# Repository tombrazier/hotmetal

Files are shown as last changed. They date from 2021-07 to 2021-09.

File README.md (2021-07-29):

# Hot Metal Brewbot

This project started as an Arduino PID controller for my coffee machine and gradually became a lot more. Read about it [here](http://tomblog.firstsolo.net/index.php/hobbies/pimping-my-coffee-machine/). See a video of the machine in action [here](https://www.youtube.com/watch?v=up54jM5fQOQ).

Presently there is just a controller PCB and firmware. In time I plan to build a front panel PCB as well. The board is designed to mount neatly in a Gaggia Baby machine but there is scope for other layouts for different machines. The circuit diagram would work with pretty much all machines with some modifications to the firmware.

`hardware/controller` contains EAGLE CAD files for the controller PCB which is an Arduino Nano shield.

`hardware/schematics` contains PDFs of the schematics for release versions of the controller. Saves hacing to have EAGLE installed and also gives past versions.

`firmware/controller` contains the Arduino source code.

`hardware/controller/DesignNotes.txt` contains a lot of useful information as well as notes about what needs doing next.

The present revision of my controller is 2.0, but I already know of some things I would like to change in 2.1. `DesignNotes.txt` documents these.

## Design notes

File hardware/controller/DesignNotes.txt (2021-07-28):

CHECKS before send board to print
---------------------------------
Y is board labeled with name and revision?
Y make sure all text is vector font (Options->User Interface->Always use vector fonts. Because Eagle stupidly offers proportional font it cannot render to gerber files!)
Y check ERC
Y set up DRC rules (using JLCPCB for fab?)
Y renumber components
N check that track layout and board mounting prevent a water leak from conducting live to the user
Y check through-hole components are on the right side of the board (top, i.e. not mirrored)
Y check label placements (not covered by components or clashing with each other)
Y check labels are not covering pads
Y check labels are on the correct layer (i.e. blabel / tlabel)
Y check pins are labelled where necessary (incl Live, Neutral, Earth)
Y check component sizes vs stock (e.g 1uF 0603 ceramic cap)
Y check the specific components are available to buy (e.g. regulators)
Y check USB cable clearance (11mm above board, 9.8mm wide, 28mm long)
Y check IO pins are on a 0.1" grid
Y check heatsink placements
Y check no components that collide with the vertical columns on machine base plate back side (0.8" to 1.1" and 2.8" to 3.1" from bottom right, height 0.8")
Y check no components that collide with the vertical columns on machine base plate front side (3.45" to 3.7" from bottom right, height 0.6")
Y check all airwires routed (Tools -> Statistics gives number of unrouted airwires)
Y check mains power nets are in net class power (see what breaks min width 50mil and 1.6mm separation from default class and 1mm separation for power class)
Y check DRC (with appropriate layers visible otherwise they don't get checked - note label layers are best checked visually and stop layers should be checked)

Errors/notes:
-------------
-Space for an onboard fuse? (For Non-UK plugs).
-Onboard varistor.
-D2 is physically close to the tray and a deep pool of water could connect to mains. Exposed GND along
 top and bottom sides of the board at the lower edge (in HEATSINK component) would mitigate as well.)
-Move zero cross circuit to 9V side of transformer and use JFET! (MMBFJ201 would need no resistor).
 -R43 should be 1206 not 0805 to handle 400V.
 -The R43 / C26 RC circuit is really an RLC circuit when stray (e.g. house) inductance is taken into account and
  can have inductance in the 10s of uH. If the circuit is underdamped, this can result in destructive voltage spikes.
-PMPSW and STMSW are wrong way round considering line to IC2. Also it's a lot easier if software
 controls the temperature probe ranges so use D10 (SS) pin for PMPSW.
-Buzzer FET should have gate pulldown for when AVR is resetting and pin output is open.
-R10/R11 potential divider relies on 5V which is unreliable, e.g. when on USB - use zener or regulator or something
 (MMBFJ201 if using it for zero crossover)
-There is never a need for VSS < 0V even with K type. Eliminate -ve supply.
-Since VDD > 5V (i.e. arduino VCC), opamp outputs to the arduino should have resistors on them.
-Coupling between VSS / VDD and the inputs to the opamp. Route lines differently.
 -Piezo buzzer puts noise on the VDD line.
 -I changed C12 to 1uF 16V and doubled up C5.
 -Since we really don't care about an high frequency signal, why not put a cap between opamp +ve and -ve inputs?
-LED markings have no polarity.
-Provision for NTC probes is poor.
-Terminal markings should be repeated on underside of board.
-The USB 5V supply can be quite noisy at highish frequency (e.g. 50kHz) and this
 noise is conducted progressively to ground in the probe pin decoupling caps and C25,
 causing a differential voltage across the probes. Only an issue when mains power off.
 Whichever of SJ1-SJ4 is used, it should be a 2k2 resistor, not a bridge.
-The AREF pins sucks in about 50uA, which makes the probe current about 5% over target
 and shifts the temperature ranges downwards a bit. Not really an issue but it means
 a nominal 100R resistor probably has an input > 0 and a 150R nominal is 1023 (i.e.
 maxes out the ADC.
-With K type probe, an additive component would allow for probe to be cooler than AVR
-With K type probe, the op amp's Vio is quite significant but results in a fixed delta. Unfortunately this varies by 7uV/C which is significant at a range or 50C. 
-With K type probe, internal temp reference is sensitive to VCC. So you get a different reading if powered by USB vs mains.
 So is bandgap, to a similar degree, divide by BG to offset the change.
-With K Type, internal temp is bady affected by self-heating of the AVR.
-With K type probe, internal temp has occasional wild excursions.

TODO:
-----
Build: make cable for Twin front panel using an Amp-TE Micro-Match 14 way ribbon connector but with 4 strands of wire.
Plastic backing plane.
internal LEDs for when front panel is perspex?

Spacing, etc. (PCBWay recommendations)
--------------------------------------

Min recommended track width: 6mil.
Min recommended spacing:     6mil.
Min drill size:              0.2mm (8mil) (but 0.3mm costs less).
Min annular ring:            0.15mm (6mil) (so total via diameter >= 0.3mm larger than hole).

Build notes
-----------

C20, C22, SJ1 to SJ7 give options to connect thermocouples or resistive
deivces (e.g. PT100 probes) to probes 1 to 3. For PT100, SJ1 and SJ5 to
SJ7 are be bridged and the rest unbriged/unpopulated. But if using
thermocouples rather than PT100s, some of the jumpers are unbridged
and some of the resistors and capacitors are populated. The resistor
network on the opamps would also have to change.

Displays
--------

OLED modules that use I2C or SPI look like a good option. E.g. the waveshare 1.5inch OLED
display. OLED and TFT displays us on the order of 30mA with all pixels illuminated.

Heat and heatsinksing
------------

Problem environment: both chambers inside the machine are spaces for
boilers and so hot environments. Depending on location, it could be as
hot as 70C.

The bottom of the board is shielded from heat by the board itself and is
also adjactent to the case. This will be the coolest spot.

High power components need to be on the bottom of the board. E.g. regulators
and constant current depletion mode FET in the zero-crossover circuit.

TRIAC thermal runaway: any temperature over 125C causes the TRIACs to
switch on permanently, which means everything will just keep getting hotter
until something burns. So TRAIC cores MUST remain < 125C. So 115C for safety.
So we have a headroom of 45K.

Current: maximum continuous power demand is when steaming milk. For a
decent flow of steam (3 nozzle), about 2kW is desirable. At 240VAC, that
means 8.3A and for TRIACs that means about 8W.

Heatsinks: the chunkiest passive heatsinks for TO-220 packages tend towards
10K/W. At a headroom of 45K, that means we can cool 4.5W. This is less than
the 8.3W we need to cool!

Solution: a happy circumstance is that continuous 8.3W power drain only
occurs when water is flowing through the machine. So, an easy answer is
to use a water-cooled CPU heatsink connected inline with the supply water.
This arrangement will need to be on some kind of bracket to keep it in place.
But the board, as a whole, need to be on a bracket to keep it in place.
A copper sheet between the heatsink and the TRAICs can have a double function
of bracket and heatpipe. Best of all, no power is wasted as the waste heat
becomes a slight preheat for the water!

Analogue sensors
----------------

Aref given by a voltage regulator:
    -Needs to be exact.
    -Needs to be stable over temperature range. Although the most important
     measurements are from the PT100 devices, which are in-line and Aref
     scales with PT100 voltage and stability isn't important.
    -If in-line with PT100 devices, adjust pin current needs to be tiny.

MCP1700T-1802E/TT has very small GND current (MOSFET device) and reasonable stability
over temperature.

Place regulator on bottom of board for minimal effect from boiler heat.

Steam switch can be used to provide an input to op-amps that shifts PT100 range.

Main boiler sensors
-------------------

These need to be the most accurate of all the sensors so we can set brew
temperature to within a fraction of a degree. The resistor network converts
the probe voltage range for 120C to a range of 1.8V (which is what Aref gets
from the 1.8V regulator) and subtracts the equivalent of 100Ohms which is
the PT100 value for 0C.

When the steam switch is closed, an analogue switch brings another resistor
into the network, subtracting an extra voltage from the output and shifting
the measurement range.

Water level gauge
-----------------

MPXV7002 works nicely.
(https://www.nxp.com/docs/en/data-sheet/MPXV7002.pdf)

The reservoir is empty when there is about 5cm head of water = 0.5kPa and
full when there is about 5cm head of water = 1.5kPa. These pressures equate
to an output voltage of 3V to 4V (at supply voltage of 5V and linearly scaled
against the supply).

Variations in atmospheric pressure cause the max and min values to change
so we need some space around these points. If we allow a range of 2.5V to
4.5V, then 1 bit from the 10 bit ADC equates to about 0.2% of the reservoir,
which is a resultion greater than measurement error.

Vref is attached to 1.8V which implies the need for a gain of less than unity,
which makes op-amp instability likely. We can acheive this with a potential
divider to zero on both +ve and -ve inputs to the op amp.

                  |\
Vp ---[ R1 ]------|+\
GND---[ R2 ]-'    |  \______Vo
                  |  /    |
5v ---[ R3 ]------|-/     |
GND---[ R4 ]-|    |/      |
             L---[ R5 ]---'

R1=100k, R2=10k, R3=100k, R4=4k7, R5=33k gives a pretty good range from
Vp = 2.17V to 4.54V.

Zero-crossover
--------------

The zero-crossover circuit uses a diode in series with an opto-coupler to
signal from the mains voltage side to the logic voltage side that mains
is above a few volts. The opto-coupler is connected directly to an arduino
pin with an internal pull-up.

This has a nice advantage that the on and off times are slightly different
because mains voltage has to be about two diode drops above zero for the
opto-coupler to switch on enough. With suitable calibration, mains voltage
can therefore be measured, which can make power calculations even more accurate.
This is overkill and, therefore, strictly bad software engineering but it
feels strangely pleasing!

To keep the components safe, a depletion mode MOSFET and a resistor act
as a current-limiting circuit to keep the current below around 0.5mA.

The circuit as a whole needs to be protected from high frequency noise for
two reasons. First, noise can cause a zero-crossover in the wrong place.
Much more seriously, a high dV/dt on the MOSFET can destroy it.

There are two ways a MOSFET can be damaged by dV/dt. One is to do with the
parasitic BJT in combination with its base resistances and capacitances. This
is a hard limit of the device itself. The datasheet give a max of 6GV/s.

The other source of damage is when the maximum Vgs voltage is exceeded because
of gate capacitances. This depends on the device and also the external circuit.
In our circuit, a sudden change of voltage from operating the mains switch
mid-cycle is enough to cause this. It can happen with switching on or
off. Technical: mains voltage is applied across drain and gate with a resistor
between gate and source. The normal current path goes through this resistor.
But if there is a sudden 340V change on Vgd then the Cds and Cgs have to charge
to this voltage. According to the datasheet, Cds = Coss - Crs = 1.4pF and
Cgs = Ciss - Crss = 20pF. The voltage on source will change by 340 / (1 + Cgs / Cds)
with respect to gate which is about 22V. The absolute maximum Vgs is +/- 20V.

We can limit Vgs to +/-20V if we limit the current in the 2k2 gate source resistor
to about 9mA. For Cds to conduct that current, voltage across Cds has to be
changing at about 6.5GV/s. This is more than the datasheet's hard limit of 6GV/s, so
6GV/s is the limit.

A series RC filter can give this but can also introduce problems of its own.
Taking stray inductance into account, we have an RLC circuit. Depending on
the initial charge of the capacitor and the instantaneous mains voltage applied,
there can be oscillations that peak a lot higher than the mains voltage peak.
Worst case scenario, at -340V transformer stops conducting because bridge rectifier
on 9V side switches off and zero-cross circuit is reverse biased. Capcitor remains
charged to -340V and then 340V is applied. The resistor has to handle 680V and the
capacitor voltage swings to as much as 1020V! With just the right timing in switch
bounce this could happen!

Nonetheless, if switch on occurs at 340V and the RLC circuit is not well damped
then the initial oscillation can swing the voltage on the capacitor up to nearly 680V!
So the RLC circuit should be overdamped. i.e. R^2 > 4L/C. L can be as high as tens of
uH for 10m of copper wire - which is normal in house wiring.

A 100R resistor in series with a 500V 68nF capacitor will keep dV/dt low enough
and also easily overdamp a house with 100uH inductance in the wiring.

Better solution: move the zero-crossing circuit to the 9V side of the transformer
and use a JFET instead of a MOSFET and a schottkey diode for protection.

Arduino pins
------------

Avoid using the SDA and SCL (A4 and A5) pins so TWI is available (leave as general digital IO).
Avoid using the SS, MISO, MOSI and CLK pins so SPI is available (leave as general analogue IO).

The pump is driven by PWM, and needs to be on pin OC2B.
The solenoid can be on any digital pin as it is simply switched on and off.
The 2 boilers can be on any digital pin because they are driven by an interrupt function at each zero-crossover.
The 2 switches and 2 LEDs can be on any digital pin.
The analogue inputs should use at least pins A6 and A7 because these have no other function. There are three temp probes and a water level meter.
The flow meter can be on any pin with PCINT. Note: it's easier not to share these interrupts.
The mains zero crossover can be on any pin with PCINT. Note: it's easier not to share these interrupts.

Power supply
------------

Rev 1.0 draws around 70mA at its highest drain. Add another 8mA for the extra opto-couple
in Rev 2.0 and another 40mA for the mood lighting LEDs and we need about 120mA.

For interfacing with the Baby Twin's hardware, we need another 78mA. The
front panel uses 75mA with all LEDs illuminated and the hall effect sensor
(steam switch) uses 3mA.

A home made front panel would need something like 30mA per OLED or TFT display
and 20mA for an arduino. So 80mA.

On the plus side, removing the Baby Class front panel takes us down two LEDs
or 20mA.

So the heaviest load I imagine is 120mA plus about 80mA for a front panel
minus 20mA. We need to be able to cover 180mA comfortably.

Under maximum current on Rev 1.0, the ripple dips to just under 9V. Rev 2.0's schottkey bridge
rectifier drops less voltage than Rev 1.0's oversized 400V 1A S1G rectifier. Rev 2.0 uses a
bridge rectifier whereas Rev 1.0 used a single diode for single-phase rectification
(which made the Rev 1.0 zero-crossover circuit possible - Rev 2.0 has a different arrangement). So
the same capacitance on Rev 2.0 will give half the ripple at the same current as Rev 1.0.

We need a minimum of about 8.5V for the 8V regulator's dropout.

We can suppose, based on the above, that 1000uF will drop to 9V at 140mA. Another 50mA would
drop the 1000uF capacitor by 0.5V in 10ms. So we should be able to get 190mA. That's
okay.

TRIACs
------

Temperature inside top housing gets to as much as 50K above ambient, i.e.
in the 70s C.

Max temp for TRIAC is 125C.

Requirements for TRIACs / SCRs:
    -Isolated tab.
    -Blocking voltage > +-340V.
    -Current limit high enough.
    -Power dissipation small enough (see note).

Boiler SCR power note:
    RMS boiler current is mains voltage over resistance:
        Ib(RMS) = 240 / 21.5 = 11.2A
        Ib(AV) = Ib(PEAK) * 0.637 = Ib(RMS) * 1.414 * 0.637 = 10.1A
    Each SCR only conducts for half of each AC cycle so:
        I(RMS) = Ib(RMS) * 0.707 = 7.9A
        I(AV) = Ib(AV) / 2 = 5.0A
    That's assuming the datasheet gives power over the whole AC cycle even
    though an SCR conducts for only up to half the cycle. If it gives power
    just for the half-cycle where it conducts, then we need to read off power
    against the full current (RMS or AV) and halve it.

For the boiler, the gate of the SCR needs to be protected from negative
bias by a diode. Given this, we could just as well use a TRIAC if it is
convenient to do so.

For all the TRAICs / SCRs, the gate's current needs to be limited with a
resistor. A potential divider is unneccesary, though, because gate/cathode
is a PN juntion (i.e. a diode) and so it's voltage is limited to the diode
turn on voltage.

For the boiler:
TXN612 SCR is insulated, blocks 600V, carries 8A average and generates 6W at I(AV)=5A.
BTA24-600BWRG or BTA24-800BWRG TRIACs also meet all the criteria for the boiler.

For pump and solenoid:
BTA08-600CWRG TRIAC is sufficient and insulated.

Gaggia Baby Twin front panel interface
--------------------------------------

Note: for testing purposes, the Twin controller board has an 8 pin header which
includes a GND pin:

    JP7
    -  -
    -  -
    -  -
    -  - GND

A 14 wire ribbon cable connects the front panel to the controller board. If we
number the wires from 1 to 14, starting at the red end, then the connector
on the board alternates sides:

14  12  10   8   6   4   2
 |   |   |   |   |   |   |
-----------------------------
|                           ]
|                          |
|                           ]
-----------------------------
   |   |   |   |   |   |   |
  13  11   9   7   5   3   1

The connector is from te (Tycho Electronics) and the ribbon cable part
number is 1-215083-4 or 8-215083-4 (same part but one comes in boxes and
the other on reels).

My best guess is that the controller board has two interfaces on this cable,
one for the Twin and one for the Dose. For the Twin, it is a TWI interface
and for the Dose it is a simple set of lines to LEDs and switches. The only
pins that seem to make any difference for the Twin are:

1  VCC
9  SDA
7  Button touch notification
11 SCL
14 GND

The front panel pulls pins 9 (SDA), 11 (SCL) and 7 high. When a button is
touched or released, pin 7 pulses low for 50us. This could be used to respond
or you can you poll regularly.

In addition, the controller board pulls the following high: 2, 4, 6, 8, 10.
And 3 and 5 are high impedence. And 12 is low or high impedence (can't remember).
None of these are relevant to the Twin front panel.

The controller polls the front panel periodically with the following protocol:
Poll rate: normally every 48ms. When a button is being touched, continuously.
SCL clock speed: 62500Hz.

At each poll, the controller writes the LED state and then reads the buttons.

To write: write two bytes, the first is address and the second is value.
To read: write one byte (address) and read one byte (value).
The front panel only responds to the general call TWI address 0.
The address of the LEDs is 0x00 and the address of the buttons is 0x01.

So on the TWI bus, you see:
START, address packet to 0 and W = 0x00, 2 data packets: 0x00, CODE1, STOP,
START, address packet to 0 and W = 0x00, 1 data packets: 0x01, STOP,
START, address packet to 0 and R = 0x01, 1 data packets: CODE2, STOP.

CODE1 is a six bit bitmask plus two parity bits:

| 7        | 6        | 5           | 4         | 3         | 2          | 1         | 0         |
| Parity 1 | Parity 0 | Element LED | Steam LED | Water LED | Manual LED | 2 cup LED | 1 cup LED |

Parity 1 is bit3 XOR bit4 XOR bit5.
Parity 0 is bit0 XOR bit1 XOR bit2.

CODE2 is a pair of 4 bit nibbles where high nibble = 1s complement of low nibble.
Low nibble is a 4 bit bitmask indicating which button is touched:

| 3     | 2      | 1     | 0     |
| Water | Manual | 2 cup | 1 cup |

Note: if more than one button is touched, this is invalid and code2 = 0xf0.

Front panel dimensions
----------------------

outer rect wxh: 108x68
this includes a 2.5mm deep tab at the top which is 6mm high
tabs on sides: 16 to 27 mm from bottom
inner rect wxhxd: 93.5x79x3
circle dia x d: 78x1.4

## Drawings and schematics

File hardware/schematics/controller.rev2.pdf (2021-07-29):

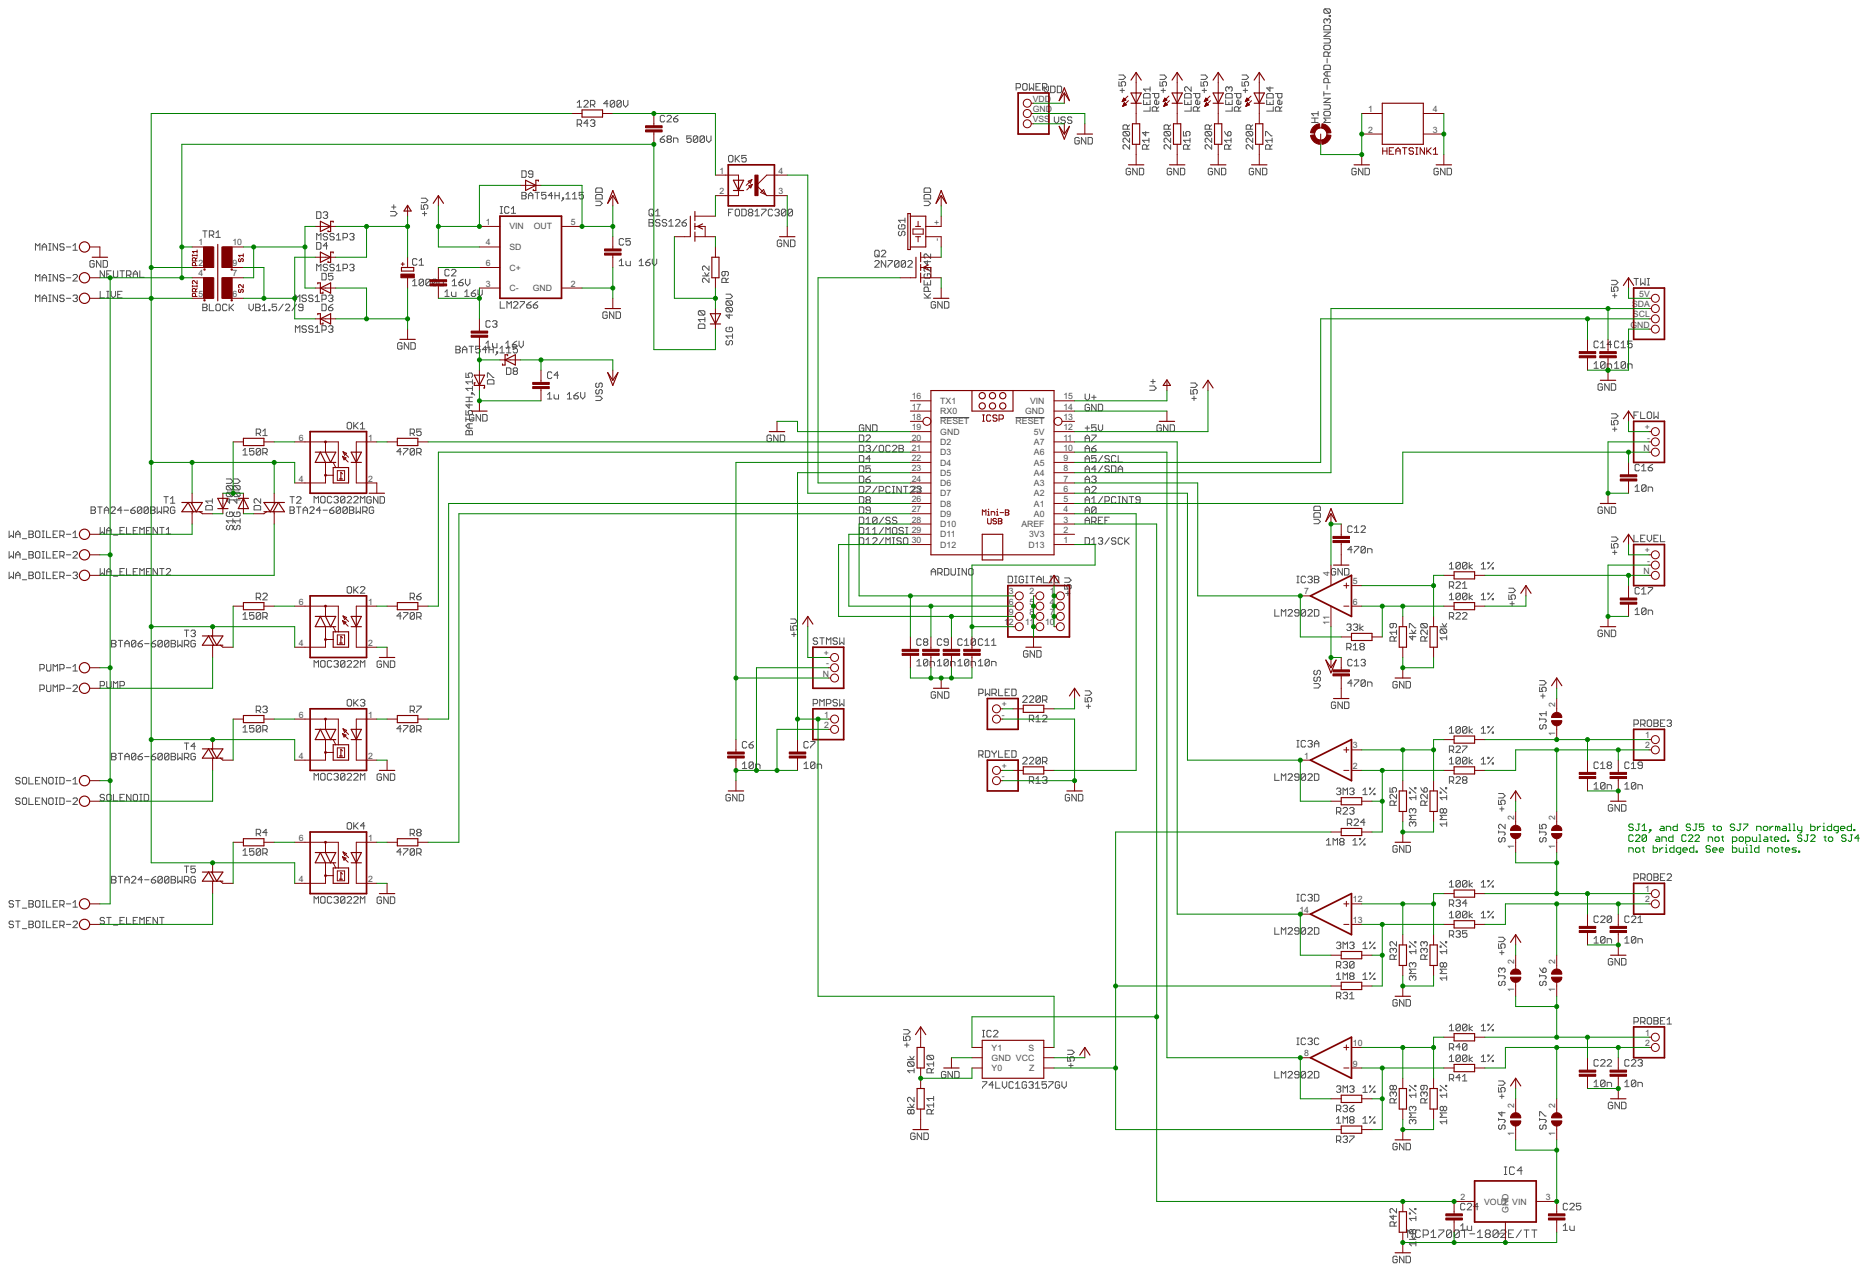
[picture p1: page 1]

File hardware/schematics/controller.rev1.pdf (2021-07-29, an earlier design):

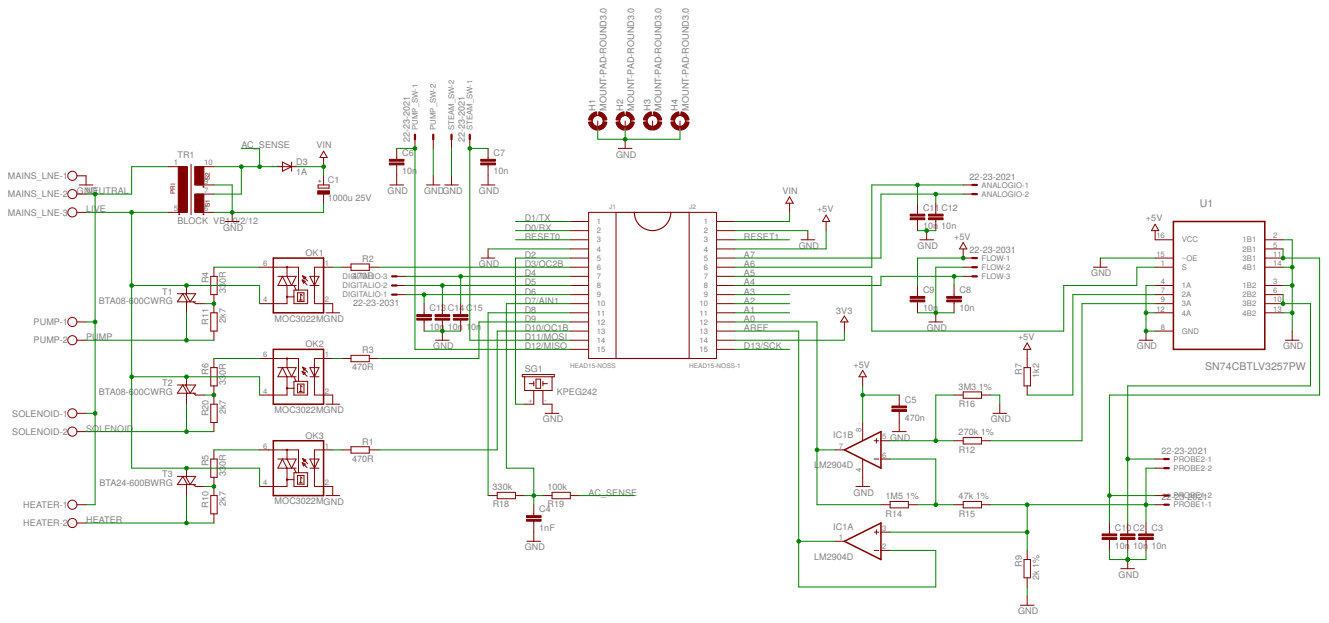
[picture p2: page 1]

MOUNT-PAD-ROUND3.0 MOUNT-PAD-ROUND3.0

1 | 14

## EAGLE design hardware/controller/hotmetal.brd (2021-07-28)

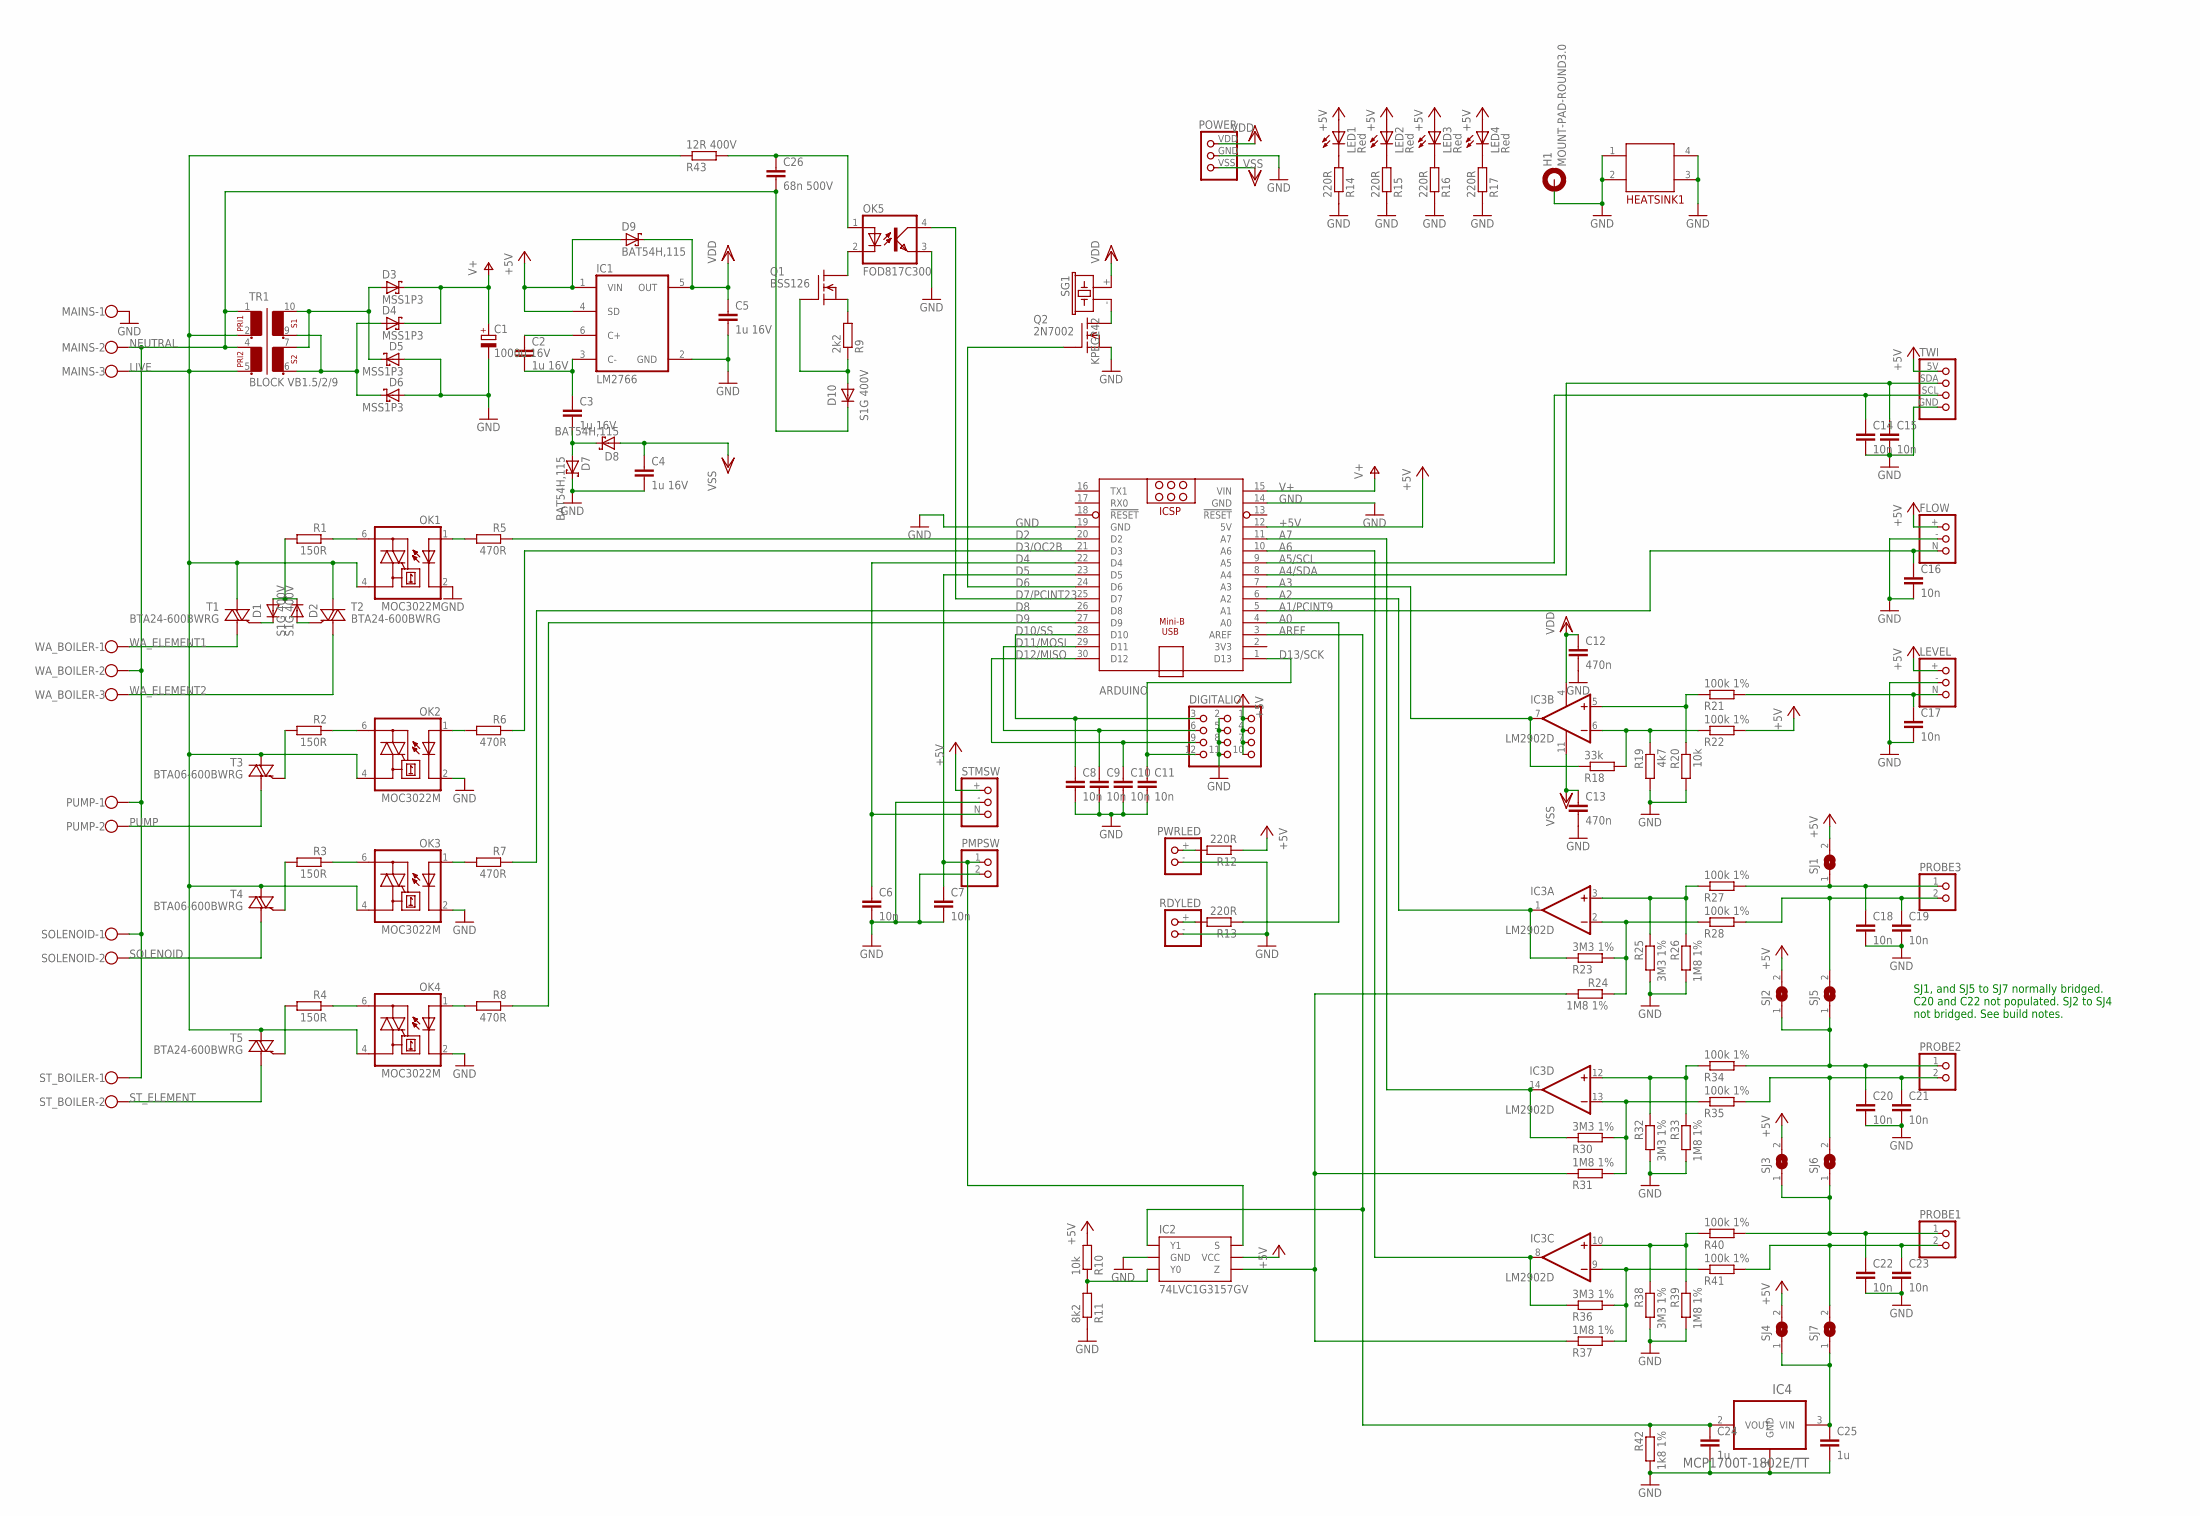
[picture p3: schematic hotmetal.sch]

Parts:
ARDUINO: ARDUINO_NANO
C1: 1000u 16V; E5-10,5
C2, C3, C4, C5: 1u 16V; C0603K
C6, C7, C8, C9, C10, C11, C14, C15, C16, C17, C18, C19, C20, C21, C22, C23: 10n; C0603K
C12, C13: 470n; C0603K
C24, C25: 1u; C0603K
C26: 68n 500V; C1210K
D1, D2, D10: S1G 400V; DO214AC
D3, D4, D5, D6: MSS1P3; POWERDI323
D7, D8, D9: BAT54H,115; SOD123F
DIGITALIO: HDR4X3PWR
FLOW: HDR3PWR
H1: MOUNT-PAD-ROUND3.0; 3,0-PAD
HEATSINK1: HOTMETALHEATSINK
IC1: LM2766; SOT23-6
IC2: 74LVC1G3157GV; SOT457
IC3: LM2902D; SO14
IC4: MCP1700T-1802E/TT; SOT23
LED1, LED2, LED3, LED4: Red; SML0805
LEVEL: HDR3PWR
MAINS: W237-103
OK1, OK2, OK3, OK4: MOC3022M; DIL06
OK5: FOD817C300; DIL04
PMPSW: HDR2
POWER: HDR3VDDVSS; HDR2VDDVSS
PROBE1, PROBE2, PROBE3: HDR2
PUMP: W237-102
PWRLED: HDR2PWR
Q1: BSS126; SOT23
Q2: 2N7002; SOT23
R1, R2, R3, R4: 150R; 0204/7
R5, R6, R7, R8: 470R; R0805
R9: 2k2; R0805
R10, R20: 10k; R0805
R11: 8k2; R0805
R12, R13, R14, R15, R16, R17: 220R; R0805
R18: 33k; R0805
R19: 4k7; R0805
R21, R22, R27, R28, R34, R35, R40, R41: 100k 1%; R0805
R23, R25, R30, R32, R36, R38: 3M3 1%; R0805
R24, R26, R31, R33, R37, R39: 1M8 1%; R0805
R42: 1k8 1%; R0805
R43: 12R 400V; R0805
RDYLED: HDR2PWR
SG1: KPEG242; F/CM12P
SJ1, SJ2, SJ3, SJ4, SJ5, SJ6, SJ7: SJ
SOLENOID: W237-102
STMSW: HDR3PWR
ST_BOILER: W237-102
T1, T2, T5: BTA24-600BWRG; TO220FACEDOWN
T3, T4: BTA06-600BWRG; TO220FACEDOWN
TR1: BLOCK VB1.5/2/9; T2P2S
TWI: HDR4TWI
WA_BOILER: W237-103

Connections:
+5V: ARDUINO.12 (5V), D9.A, DIGITALIO.1, DIGITALIO.4, DIGITALIO.7, DIGITALIO.10, FLOW.+ (1), IC1.1 (VIN), IC1.4 (SD), IC2.5 (VCC), LED1.A, LED2.A, LED3.A, LED4.A, LEVEL.+ (1), R10.2, R12.1, R22.2, SJ1.2, SJ2.2, SJ3.2, SJ4.2, STMSW.+ (1), TWI.5V (1)
A0: ARDUINO.4 (A0), R13.1
A1/PCINT9: ARDUINO.5 (A1), C16.1, FLOW.N (3)
A2: ARDUINO.6 (A2), IC3.1 (OUT), R23.1
A3: ARDUINO.7 (A3), IC3.7 (OUT), R18.1
A4/SDA: ARDUINO.8 (A4), C15.1, TWI.SDA (2)
A5/SCL: ARDUINO.9 (A5), C14.1, TWI.SCL (3)
A6: ARDUINO.10 (A6), IC3.8 (OUT), R36.1
A7: ARDUINO.11 (A7), IC3.14 (OUT), R30.1
AREF: ARDUINO.3 (AREF), C24.1, IC2.1 (Y1), IC4.2 (VOUT), R42.1
D2: ARDUINO.20 (D2), R5.1
D3/OC2B: ARDUINO.21 (D3), R6.1
D4: ARDUINO.22 (D4), C6.1, STMSW.N (3)
D5: ARDUINO.23 (D5), C7.1, IC2.6 (S), PMPSW.1
D6: ARDUINO.24 (D6), Q2.1 (G)
D7/PCINT23: ARDUINO.25 (D7), OK5.4 (COL)
D8: ARDUINO.26 (D8), R7.1
D9: ARDUINO.27 (D9), R8.1
D10/SS: ARDUINO.28 (D10), C8.1, DIGITALIO.3
D11/MOSI: ARDUINO.29 (D11), C9.1, DIGITALIO.6
D12/MISO: ARDUINO.30 (D12), C10.1, DIGITALIO.9
D13/SCK: ARDUINO.1 (D13), C11.1, DIGITALIO.12
GND: ARDUINO.14 (GND), ARDUINO.19 (GND), C1.-, C4.2, C5.2, C6.2, C7.2, C8.2, C9.2, C10.2, C11.2, C12.2, C13.2, C14.2, C15.2, C16.2, C17.2, C18.2, C19.2, C20.2, C21.2, C22.2, C23.2, C24.2, C25.2, D5.A, D6.A, D7.C, DIGITALIO.2, DIGITALIO.5, DIGITALIO.8, DIGITALIO.11, FLOW.- (2), H1.B3,0, HEATSINK1.1, HEATSINK1.2, HEATSINK1.3, HEATSINK1.4, IC1.2 (GND), IC2.2 (GND), IC4.1 (GND), LEVEL.- (2), MAINS.1, OK1.2 (C), OK2.2 (C), OK3.2 (C), OK4.2 (C), OK5.3 (EMIT), PMPSW.2, POWER.GND (2), PWRLED.- (2), Q2.2 (S), R11.1, R14.1, R15.1, R16.1, R17.1, R19.2, R20.2, R25.2, R26.2, R32.2, R33.2, R38.2, R39.2, R42.2, RDYLED.- (2), STMSW.- (2), TWI.GND (4)
LIVE: MAINS.3, OK1.4 (A1), OK2.4 (A1), OK3.4 (A1), OK4.4 (A1), R43.1, T1.T2 (A2), T2.T2 (A2), T3.T2 (A2), T4.T2 (A2), T5.T2 (A2), TR1.2, TR1.5
unnamed: OK3.1 (A), R7.2
unnamed: OK1.1 (A), R5.2
unnamed: OK4.1 (A), R8.2
unnamed: R3.2, T4.G
unnamed: OK3.6 (A2), R3.1
unnamed: D1.A, D2.C, R1.2
unnamed: R4.2, T5.G
unnamed: OK4.6 (A2), R4.1
unnamed: OK1.6 (A2), R1.1
unnamed: C21.1, PROBE2.2, R35.2, SJ6.2
unnamed: C22.1, PROBE1.1, R40.2, SJ3.1, SJ6.1
unnamed: C20.1, PROBE2.1, R34.2, SJ2.1, SJ5.1
unnamed: IC3.3 (+IN), R25.1, R26.1, R27.1
unnamed: D1.C, T1.G
unnamed: D2.A, T2.G
unnamed: C17.1, LEVEL.N (3), R21.2
unnamed: IC3.10 (+IN), R38.1, R39.1, R40.1
unnamed: IC3.9 (-IN), R36.2, R37.2, R41.1
unnamed: Q2.3 (D), SG1.- (2)
unnamed: LED3.C, R16.2
unnamed: C2.1, IC1.6 (C+)
unnamed: OK2.1 (A), R6.2
unnamed: R2.2, T3.G
unnamed: OK2.6 (A2), R2.1
unnamed: PWRLED.+ (1), R12.2
unnamed: R13.2, RDYLED.+ (1)
unnamed: C2.2, C3.1, IC1.3 (C-)
unnamed: C23.1, PROBE1.2, R41.2, SJ7.2
unnamed: C26.1, OK5.1 (A), R43.2
unnamed: D10.A, Q1.1 (G), R9.1
unnamed: C19.1, PROBE3.2, R28.2, SJ5.2
unnamed: C18.1, PROBE3.1, R27.2, SJ1.1
unnamed: IC3.12 (+IN), R32.1, R33.1, R34.1
unnamed: IC3.2 (-IN), R23.2, R24.1, R28.1
unnamed: IC3.13 (-IN), R30.2, R31.2, R35.1
unnamed: IC3.5 (+IN), R20.1, R21.1
unnamed: IC2.3 (Y0), R10.1, R11.2
unnamed: IC2.4 (Z), R24.2, R31.1, R37.1
unnamed: D3.A, D5.C, TR1.7, TR1.10
unnamed: IC3.6 (-IN), R18.2, R19.1, R22.1
unnamed: C25.1, IC4.3 (VIN), SJ4.1, SJ7.1
unnamed: LED1.C, R14.2
unnamed: LED2.C, R15.2
unnamed: LED4.C, R17.2
unnamed: D4.A, D6.C, TR1.6, TR1.9
unnamed: Q1.2 (S), R9.2
unnamed: OK5.2 (C), Q1.3 (D)
unnamed: C3.2, D7.A, D8.C
NEUTRAL: C26.2, D10.C, MAINS.2, PUMP.1, SOLENOID.1, ST_BOILER.1, TR1.1, TR1.4, WA_BOILER.2
PUMP: PUMP.2, T3.T1 (A1)
SOLENOID: SOLENOID.2, T4.T1 (A1)
ST_ELEMENT: ST_BOILER.2, T5.T1 (A1)
V+: ARDUINO.15 (VIN), C1.+, D3.C, D4.C
VDD: C5.1, C12.1, D9.C, IC1.5 (OUT), IC3.4 (V+), POWER.VDD (1), SG1.+ (1)
VSS: C4.1, C13.1, D8.A, IC3.11 (V-), POWER.VSS (3)
WA_ELEMENT1: T1.T1 (A1), WA_BOILER.1
WA_ELEMENT2: T2.T1 (A1), WA_BOILER.3

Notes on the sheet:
SJ1, and SJ5 to SJ7 normally bridged. C20 and C22 not populated. SJ2 to SJ4 not bridged. See build notes.

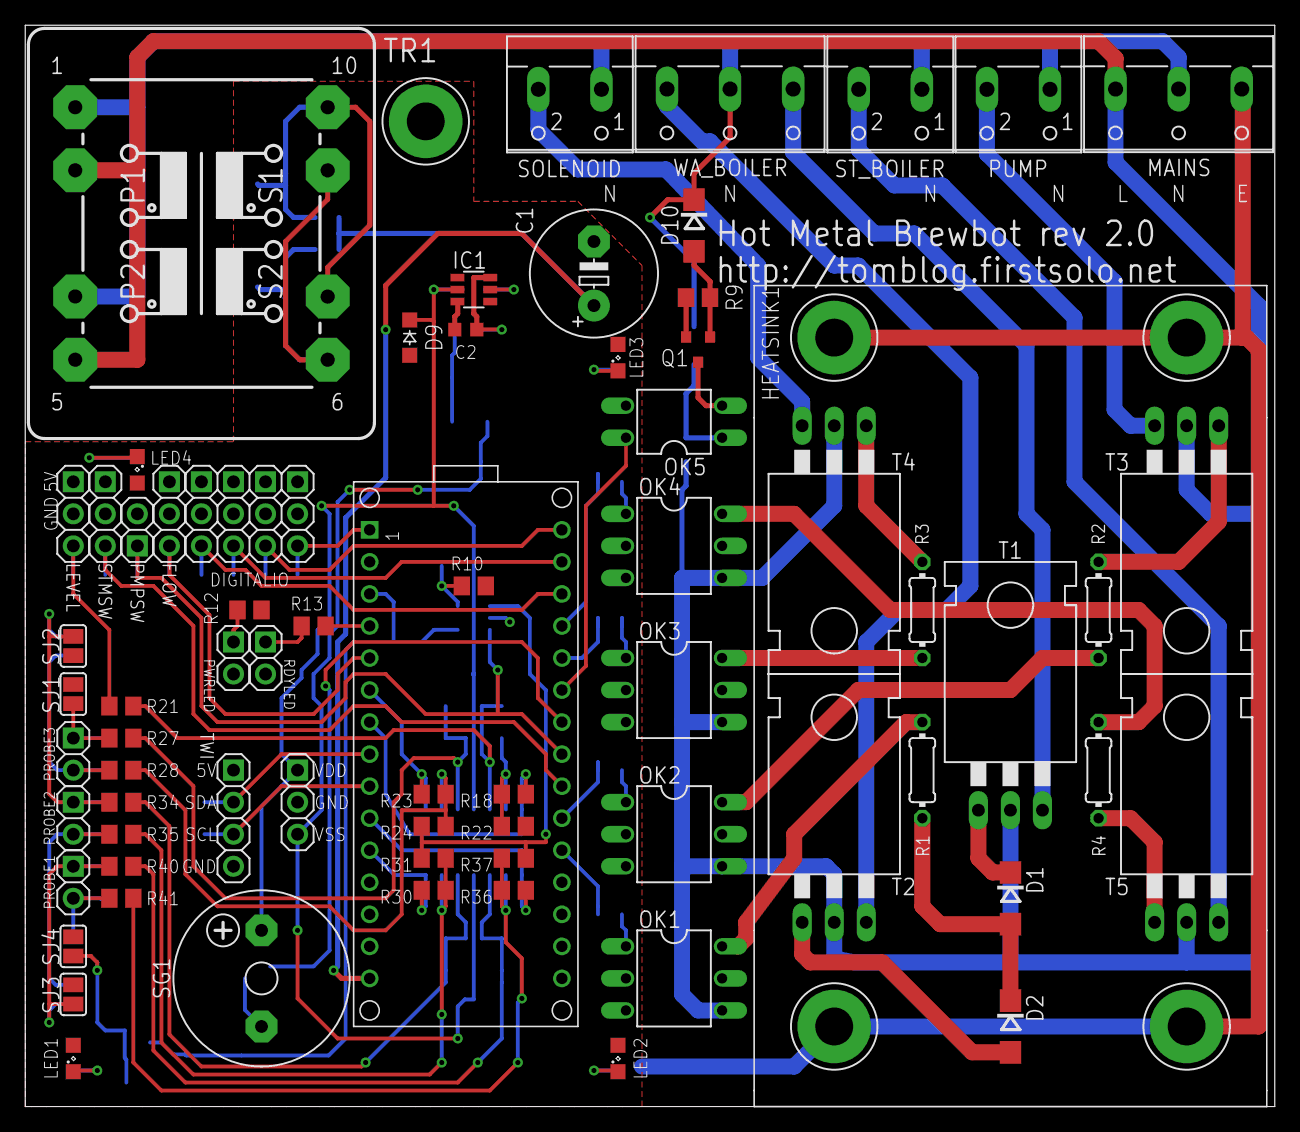
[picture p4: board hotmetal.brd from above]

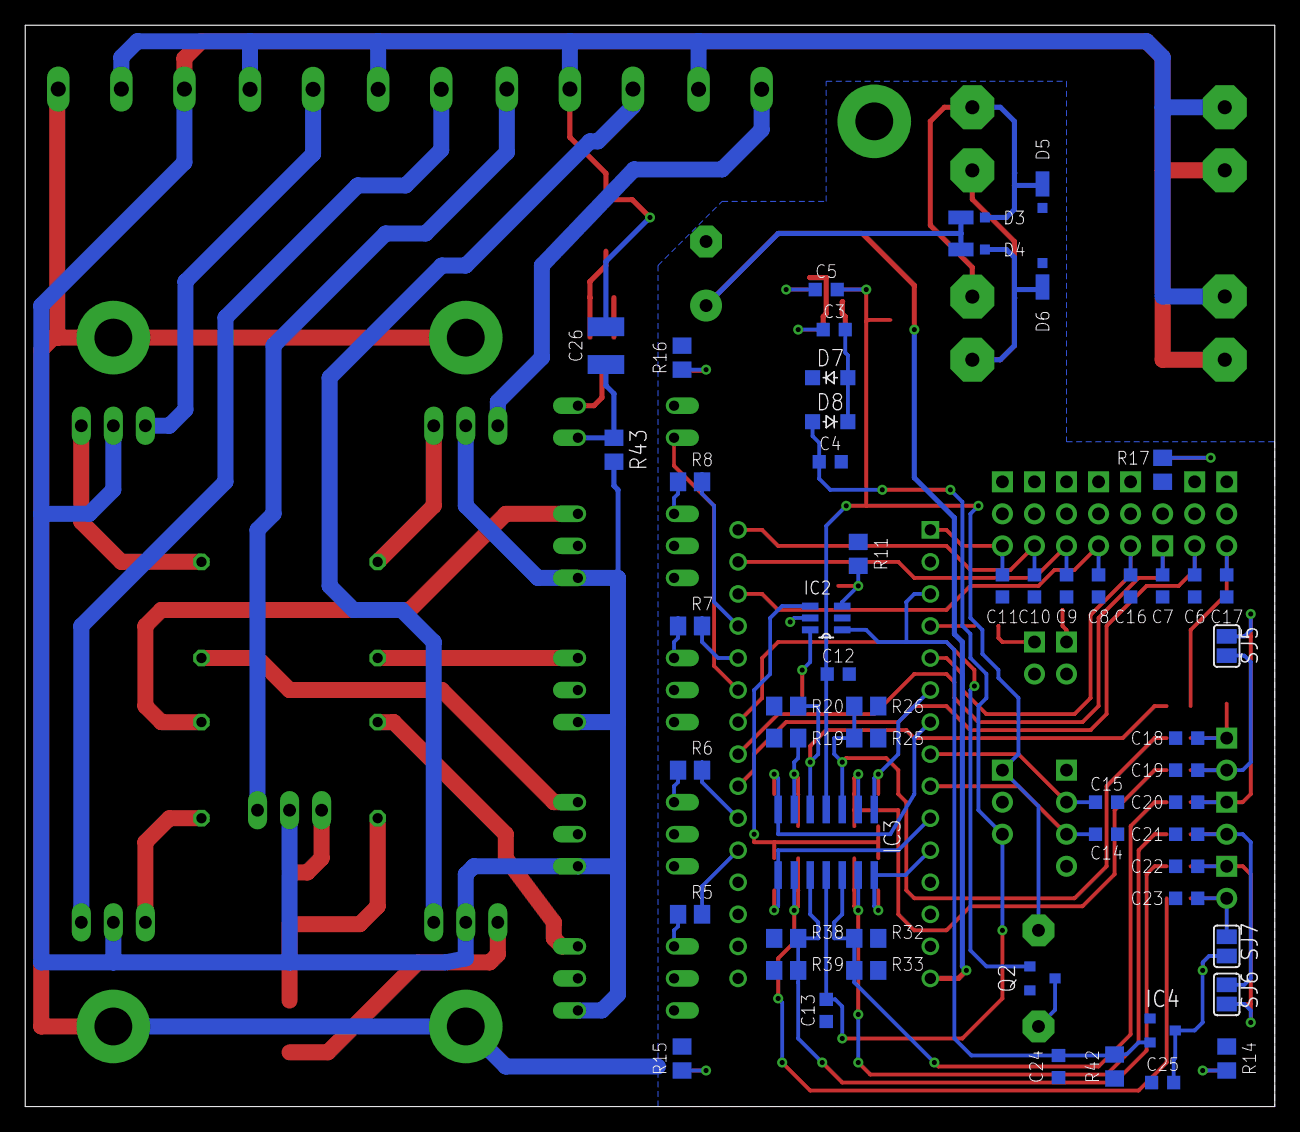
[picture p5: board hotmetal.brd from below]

Board: 2 copper layers, 99.1 x 85.7 mm, 127 parts (56 on the bottom side), 81 nets.

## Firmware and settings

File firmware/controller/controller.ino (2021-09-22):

/*
 *     Copyright (C) 2010-2020 Tom Brazier (http://tomblog.firstsolo.net)
 *     
 *     This file is part of Hot Metal Brewbot.
 *     
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
 *     You should have received a copy of the GNU General Public License
 *     along with Hot Metal Brewbot .  If not, see <https://www.gnu.org/licenses/>.
 */

#include "constants.h"
#include "mainssync.h"
#include "flowmeter.h"
#include "analogio.h"
#include "simpleio.h"
#include "calibration.h"

// NOTE: the timing assumes the CPU main clock speed is 8Mhz or 16Mhz
// NOTE: serial port runs at 38400
// NOTE: your starting point is constants.h, which controls everything

// TODO:
// -implement steam boiler input / output
// -protect pump from overheating by preventing it from running for too long or on an empty tank (zero flow)
// -if there is a temperature probe problem, use a beep warning code
// -model water xfer coeff getting as high as 40 when at full flow
// -measure mains AC voltage to better control power
// -single cup steam mode: lower temperature?
// -track boiler volume (it's full when pump stalls and empties in steam mode at rate of power/LATENT_HEAT_VAPORISATION_100) and fill when needed instead of pulsing the pump
// -inject water more gently in steam mode (but how? maybe use full mains pulses but not every pulse like boiler?)
// -should we model heat transfer from water to brewhead and vice versa? (maybe not, it isn't right at present but it works)

void setup()
{
  // All pins should initially be high-impedance inputs. Any pins not explicitly initialised
  // below (i.e. unconnected pins) should be set to pull-up inputs. We set this up, but
  // disable pull-ups until the end of the initialisation.
  MCUCR |= _BV(PUD);
  DDRB = 0x00;
  DDRC = 0x00;
  DDRD = 0x00;
  PORTB = 0xff;
  PORTC = 0xff;
  PORTD = 0xff;

  // set up all the hardware
  MainsSyncManager::initialise();
  FlowMeter::initialise();
  AnalogIo::initialise();
  SimpleIo::initialise();

  // now setup is done, enable pullups
  MCUCR &= ~_BV(PUD);

  // set up comms
  Serial.begin(115200);

  // wait for mains zero-crossing to stabilise, but don't hold off starting the heating process
  while(!MainsSyncManager::ready())
  {
    double temperature = AnalogIo::getAvgTemperature();
    MainsSyncManager::setHeaterPower(!isnan(temperature) && temperature < BREW_SETPOINT ? SAFE_HEATER_POWER : 0.0);
  }
  MainsSyncManager::setHeaterPower(0.0);
}

void loop()
{
  // print hello world message
  Serial.println();
  Serial.println(F("Arduino Gaggia controller."));
#ifdef CALIBRATION_CODE
  Serial.println(F(" Type 'C' to enter calibration mode."));
#endif // CALIBRATION_CODE

  // clever trick: on startup, the pump switch tells us if we're in 1 cup mode and the steam switch tells us whether we're in backflush mode
  enum {BREW_1CUP, BREW_2CUP, BACKFLUSH} brewMode = BREW_2CUP;
  brewMode = SimpleIo::readPumpSwitch() ? BREW_1CUP : SimpleIo::readSteamSwitch() ? BACKFLUSH : BREW_2CUP;
  while(SimpleIo::readPumpSwitch()) delay(1);
  while(SimpleIo::readSteamSwitch()) delay(1);

  // initial value for temperature, etc.
  double shellTemp = AnalogIo::getAvgTemperature();
  if (isnan(shellTemp)) shellTemp = AMBIENT_TEMPERATURE;
  double ambientTemp = min(shellTemp, AMBIENT_TEMPERATURE);
  double elementTemp = shellTemp;
  double waterTemp = shellTemp;
  // based on heat transfer coefficients to and from brewhead, we can caluculate its steady state temp - use that
  double brewHeadTemp = (ambientTemp * BREWHEAD_AMBIENT_XFER_COEFF + shellTemp * BOILER_BREWHEAD_XFER_COEFF) / (BREWHEAD_AMBIENT_XFER_COEFF + BOILER_BREWHEAD_XFER_COEFF);
  double bodyTemp = shellTemp;
  // who knows what the triac temp is - but we can guess if we assume the triac gets to max temp when in steam mode for a long time)
  const double pcbTemp = AnalogIo::getPcbTemperature();
  double triacTemp = pcbTemp + (TRIAC_MAX_TEMPERATURE - pcbTemp) * (shellTemp - ambientTemp) / (STEAM_SETPOINT - ambientTemp);
  double pumpPowerRate = 0.0;
  double heaterPower = 0.0;

  // class to record the run state of the machine
  class State
  {
    public:
      typedef enum {BEGIN, PREHEAT_FILL, PREHEAT_HEAT, PREHEAT_VENT, PREHEAT_COOL, READY, STEAM, BACKFLUSH, BREW, INACTIVE} STATE_TYPE;
    private:
      STATE_TYPE    m_state;
      unsigned long m_lastChangeTime;
    public:
      State()
      {
        m_lastChangeTime = millis();
        m_state = BEGIN;
      }
      // set the state and return whether it had changed
      bool setState(STATE_TYPE state)
      {
        if (m_state == state) return false;
        m_lastChangeTime = millis();
        m_state = state;
        return true;
      }
      STATE_TYPE getState()
      {
        return m_state;
      }
      unsigned long millisInState()
      {
        return millis() - m_lastChangeTime;
      }
  };
  State state;

  while (true)
  {
#ifdef CALIBRATION_CODE
    // if necessary, run calibration routines
    if (Calibration::CalibrationMode()) break;
#endif // CALIBRATION_CODE

#ifdef CONTROLLER_CODE
    // read physical state
    bool steamOn = SimpleIo::readSteamSwitch();
    bool pumpOn = SimpleIo::readPumpSwitch();
    double flowRate = FlowMeter::getFlowRate();
    double waterLevel = AnalogIo::getWaterLevel();

    // control variables
    double flowSetpoint = 0.0;
    double tempSetpoint = 0.0;

    // main state machine which decides what activity we're doing and sets solenoid, flow, temperature and buzzer accordingly...
    if (state.getState() == State::BEGIN)
    {
      // at startup, go into the preheat routine unless already hot or backflushing
      if (fabs(waterTemp - BREW_SETPOINT) >= 5.0 && brewMode != BACKFLUSH)
        state.setState(State::PREHEAT_FILL);
      else
        state.setState(State::READY);
    }

    // temperature stabilisation routine: drive water through the system once at temperature (but cancel preheat if any button is pressed)
    if (state.getState() > State::BEGIN && state.getState() < State::READY)
    {
      // cancel preheat if any button is pressed
      if (steamOn || pumpOn)
        state.setState(State::READY);

      SimpleIo::switchBuzzer(false);
      SimpleIo::setTempOkayLed(false);

      if (state.getState() == State::PREHEAT_FILL)
      {
        // make sure the boiler is full by pumping against a closed solenoid valve until there is no flow
        SimpleIo::switchSolenoid(false);
        flowSetpoint = MAX_FLOW_RATE;
        tempSetpoint = STEAM_SETPOINT;

        // pump for at least half a quarter before checking flow rate and then move on if flow is less than 1.2 ml/s
        // NOTE: below 1.2 ml/s the flow meter can give very different results depending on where any bubbles
        // are in the system - indeed, it might never measure below 1 ml/s even with the minor dribble leak from the steam wand.
        // NOTE: it is an error condition if we pump for too long (maybe steam valve is open?) - give up after 20s, which
        // ought to be long enough to fill the boiler.
        if (state.millisInState() > 250 && flowRate < 1.2 || state.millisInState() > 20000)
          state.setState(State::PREHEAT_HEAT);
      }
      if (state.getState() == State::PREHEAT_HEAT)
      {
        // Open the solenoid to release pressure and heat up to the system preheat setpoint.
        // Releasing the pressure now is very important - otherwise later on we get massive and
        // unpredictable cooling as water flashes in the low pressure pulse.
        // But don't open the solenoid for too long - we don't want to cause unneccessary cooling by evaporation.
        SimpleIo::switchSolenoid(state.millisInState() < 1000);
        flowSetpoint = 0.0;
        // heat as fast as we can (but don't overshoot the steam setoint)
        tempSetpoint = STEAM_SETPOINT;
        // heat until the water is at boiling point
        if (waterTemp >= 100.0)
          state.setState(State::PREHEAT_VENT);
      }
      if (state.getState() == State::PREHEAT_VENT)
      {
        // let the steam vent until we think the brewhead is up to its asymptotic temperature
        SimpleIo::switchSolenoid(true);
        flowSetpoint = 0.0;
        tempSetpoint = STEAM_SETPOINT;
        if (brewHeadTemp >= 85.0)
          state.setState(State::PREHEAT_COOL);
      }
      if (state.getState() == State::PREHEAT_COOL)
      {
        // flow water through to cool the water and complete heating the brew head
        // stop shortly before the total boiler + water energy is right because we'll
        // need the temperatures to equalise and in the mean time, there is loss to ambient
        // experience shows 4kJ above target is where we should stop
        SimpleIo::switchSolenoid(true);
        flowSetpoint = MIN_FLOW_RATE;
        tempSetpoint = BREW_SETPOINT;
        // stop when total energy of water and boiler is right
        if ((waterTemp - BREW_SETPOINT) * SPEC_HEAT_WATER_100 * BOILER_VOLUME + ((shellTemp + elementTemp) / 2.0 - BREW_SETPOINT) * SPEC_HEAT_ALUMINIUM * MASS_BOILER_SHELL <= 4000.0)
          state.setState(State::READY);
      }
    }
    // steam state (entering steam state takes precedence over entering brew state)
    if (state.getState() == State::READY && steamOn || state.getState() == State::STEAM)
    {
      bool stateChanged = state.setState(State::STEAM);

      SimpleIo::switchBuzzer(false);

      // set the temperature to the steam temp
      tempSetpoint = STEAM_SETPOINT;

      SimpleIo::setTempOkayLed(fabs((elementTemp + shellTemp) / 2.0 - tempSetpoint) < 0.5);

      SimpleIo::switchSolenoid(false);

      // pulse pump in steam mode once a decent temperature is attained
      static bool pulsePump = false;
      if (stateChanged) pulsePump = false;
      pulsePump = pulsePump || shellTemp > STEAM_PUMP_PULSE_TEMP;
      flowSetpoint = pulsePump && (micros() % 5000000 < (unsigned long)5000000 * STEAM_PUMP_PULSE_DUTY) ? MAX_FLOW_RATE : 0.0;

      if (!steamOn)
        state.setState(State::READY);
    }
    // in backflush mode, repeatedly drive the pump until it stalls, then stop pump and close solenoid for a few seconds
    if (state.getState() == State::READY && pumpOn && brewMode == BACKFLUSH || state.getState() == State::BACKFLUSH)
    {
      bool stateChanged = state.setState(State::BACKFLUSH);

      SimpleIo::switchBuzzer(false);

      tempSetpoint = BREW_SETPOINT;

      SimpleIo::setTempOkayLed(fabs(waterTemp - tempSetpoint) < 0.5);

      static unsigned long stateChangeTime = 0;
      static bool pumping = false;
      if (stateChanged)
        pumping = true;

      if (stateChanged || pumping && flowRate > 1.2)
        stateChangeTime = micros() + BACKFLUSH_STALL_TIME;

      if ((long)micros() - (long)stateChangeTime > 0)
      {
        pumping = !pumping;
        stateChangeTime = micros() + (pumping ? BACKFLUSH_STALL_TIME : BACKFLUSH_FLUSH_TIME);
      }

      SimpleIo::switchSolenoid(pumping);
      flowSetpoint = pumping ? MAX_FLOW_RATE : 0.0;

      if (!pumpOn)
        state.setState(State::READY);
    }
    // in pump mode with 1 or 2 cup flow rate, we let the PID controller do the driving
    if (state.getState() == State::READY && pumpOn && brewMode != BACKFLUSH || state.getState() == State::BREW)
    {
      bool stateChanged = state.setState(State::BREW);

      SimpleIo::switchBuzzer(false);

      tempSetpoint = BREW_SETPOINT;

      SimpleIo::setTempOkayLed(fabs(waterTemp - tempSetpoint) < 0.5);

      // calculate total volume of shot
      static double brewStopVolume = 0.0;
      if (stateChanged)
        brewStopVolume = FlowMeter::getTotalVolume() + (brewMode == BREW_2CUP ? BREW_VOLUME_2CUP : BREW_VOLUME_1CUP);

      // now control flow and solenoid based on whether enough has been pumped through
      flowSetpoint = brewMode == BREW_2CUP ? BREW_FLOW_RATE_2CUP : BREW_FLOW_RATE_1CUP;

      // At the end of the shot, request a very low flow rate so the pressure drops
      // right off and the backflush will be negligible (doesn't really matter if we can
      // control to this, just that it is still slightly positive flow). Once the flow
      // has dropped enough, end the shot and close the solenoid valve.
      if (FlowMeter::getTotalVolume() > brewStopVolume - 5.0)
      {
        flowSetpoint = 0.25;
        if (flowRate < 0.3)
        {
          flowSetpoint = 0.0;

          // having reached the end of the shot, jump out of this state if the steam button is
          // pressed so we can enter steam state
          if (steamOn)
            state.setState(State::READY);
        }
      }
      SimpleIo::switchSolenoid(flowSetpoint > 0.0);

      if (!pumpOn)
        state.setState(State::READY);
    }
    // Guard against long periods of unuse - has the machine been left on accidentally?
    // We'll allow this for twice as long in backflush mode.
    // Also guard against the TRIAC temperature getting to unsafe levels that could cause thermal runaway which
    // should never happen unless the machine is in steam mode for a very very long time.
    if (state.getState() != State::BACKFLUSH && state.millisInState() > (unsigned long)INACTIVITY_TIMEOUT * 1000 ||
      state.millisInState() > (unsigned long)INACTIVITY_TIMEOUT * 1000 * 2 ||
      triacTemp >= TRIAC_MAX_TEMPERATURE ||
      state.getState() == State::INACTIVE)
    {
      static unsigned char switches;
      if (state.setState(State::INACTIVE))
        switches = (steamOn ? 0x02 : 0x00) | (pumpOn ? 0x01 : 0x00);

      SimpleIo::switchBuzzer(true);
      SimpleIo::switchSolenoid(false);
      SimpleIo::setTempOkayLed(false);
      flowSetpoint = 0.0;
      tempSetpoint = 0.0;

      // only exit INACTIVE state if switches change
      if (switches != ((steamOn ? 0x02 : 0x00) | (pumpOn ? 0x01 : 0x00)))
        state.setState(State::PREHEAT_FILL);
    }
    if (state.getState() == State::READY)
    {
      // complain if the reservoir is empty
      if (waterLevel < MIN_RESERVOIR_VOLUME)
        SimpleIo::switchBuzzer((millis() / 500) % 2 == 0);
      else
        SimpleIo::switchBuzzer(false);

      SimpleIo::switchSolenoid(false);
      flowSetpoint = 0.0;
      tempSetpoint = BREW_SETPOINT;

      SimpleIo::setTempOkayLed(fabs(waterTemp - tempSetpoint) < 0.5);
    }

    // control the power to the pump based on the flow rate setpoint
    if (flowSetpoint <= 0.0)
      MainsSyncManager::setPumpPower(0.0);
    else
    {
      static unsigned long lastControlTime = 0;
      double deltaTime = (double)(micros() - lastControlTime) / 1000000.0;
      double pumpPower = MainsSyncManager::getPumpPower();

      // update power 50 times per second (i.e. about once every mains cycle)
      if (deltaTime >= 0.02)
      {
        lastControlTime += deltaTime * 1000000;

        // express temperature as an error from flowSetpoint and pump_pid, which drives pumpPowerRate directly
        double error = flowRate - flowSetpoint;
        pumpPowerRate = fabs(error) * error * PUMP_PID_P;
        pumpPower += deltaTime * pumpPowerRate;
        pumpPower = min(1.0, max(0.0, pumpPower));

        // set pump power
        MainsSyncManager::setPumpPower(pumpPower);
      }
    }

    // every approx 1 second go on to manage temperature (or do so immediately if the activity has changed)
    {
      static unsigned long lastBoilerPidTime = 0;
      double deltaTime = (double)(micros() - lastBoilerPidTime) / 1000000.0;
      static double lastTempSetpoint = 0.0;
      if (lastTempSetpoint == tempSetpoint && deltaTime < 1.0) continue;
      lastTempSetpoint = tempSetpoint;
      lastBoilerPidTime += deltaTime * 1000000;

      // handle reading errors by switching the heater off and moving on
      double readTemperature = AnalogIo::getAvgTemperature();
      if (isnan(readTemperature) || readTemperature < 0.0 || readTemperature > 200.0)
      {
        Serial.println(F("Failed to read sensible temperature"));
        heaterPower = 0.0;
        MainsSyncManager::setHeaterPower(heaterPower);
      }
      else
      {
        // instead of using the temperature as read, we model the total energy and use the read value in place of one of the variables
        // this helps greatly because there is about 8s latency between applying a step change to the power and seeing a result

        // How much heat is lost to water flowing out?
        // Assumptions: 1. Water flows out at the same rate as it flows in.
        //              2. Water flowing in is at ambient temperature.
        //              3. Water enthalpies at 100°C are close enough for the other temperatures at which we operate.
        //              4. Density of water flowing in is 1;
        double waterToFlowPower = flowRate * (waterTemp - RESERVOIR_TEMPERATURE) * SPEC_HEAT_WATER_100;

        // How much power is lost to the atmosphere from the brew head?
        double brewHeadToAmbientPower = (brewHeadTemp - ambientTemp) * BREWHEAD_AMBIENT_XFER_COEFF;

        // How much power is transferred from the boiler to the water?
        double shellToWaterPower = (shellTemp - waterTemp) * BOILER_WATER_XFER_COEFF_NOFLOW / 2.0;
        double elementToWaterPower = (elementTemp - waterTemp) * BOILER_WATER_XFER_COEFF_NOFLOW / 2.0;

        static bool steamValveOpen = false;
        if (steamValveOpen || flowRate > 1.0)
        {
          shellToWaterPower = (shellTemp - waterTemp) * BOILER_WATER_XFER_COEFF_STEAM / 2.0;
          elementToWaterPower = (elementTemp - waterTemp) * BOILER_WATER_XFER_COEFF_STEAM / 2.0;
        }

        double steamHeatLoss = 0.0;
        if (SimpleIo::solenoidOn() || steamValveOpen)
        {
          // we lose exactly the right amount of heat through vaporisation that the water temp ends up being 100°C
          // which won't be exactly right - the back pressure through the nozzle will mean it's a little more than 100°C
          steamHeatLoss = (waterTemp - 100.0) * (SPEC_HEAT_WATER_100 * BOILER_VOLUME) / deltaTime + shellToWaterPower + elementToWaterPower - waterToFlowPower;
          steamHeatLoss = max(0.0, steamHeatLoss);
        }

        // How much power is transferred from the boiler to the brew head?
        double shellToBrewHeadPower = (shellTemp - brewHeadTemp) * BOILER_BREWHEAD_XFER_COEFF / 2.0;
        double elementToBrewHeadPower = (elementTemp - brewHeadTemp) * BOILER_BREWHEAD_XFER_COEFF / 2.0;
        double waterFlowToBrewHeadPower = (waterTemp - brewHeadTemp) * flowRate * SPEC_HEAT_WATER_100;
        if (brewHeadTemp < 100.0) waterFlowToBrewHeadPower += steamHeatLoss;

        double elementToShellPower = (elementTemp - shellTemp) * ELEMENT_SHELL_XFER_COEFF;

        double shellToBodyPower = (shellTemp - bodyTemp) * BOILER_BODY_XFER_COEFF / 2.0;
        double elementToBodyPower = (elementTemp - bodyTemp) * BOILER_BODY_XFER_COEFF / 2.0;

        // Now work out the temperature, which comes from power that didn't go into heat loss or heating the incoming water.
        brewHeadTemp += deltaTime * (shellToBrewHeadPower + elementToBrewHeadPower + waterFlowToBrewHeadPower - brewHeadToAmbientPower) / (SPEC_HEAT_BRASS * (MASS_BREW_HEAD + MASS_PORTAFILTER));
        waterTemp += deltaTime * (shellToWaterPower + elementToWaterPower - waterToFlowPower - steamHeatLoss) / (SPEC_HEAT_WATER_100 * BOILER_VOLUME);
        shellTemp += deltaTime * (elementToShellPower - shellToBrewHeadPower - shellToWaterPower - shellToBodyPower) / (SPEC_HEAT_ALUMINIUM * MASS_BOILER_SHELL / 2.0);
        elementTemp += deltaTime * (heaterPower - elementToShellPower - elementToBrewHeadPower - elementToWaterPower - elementToBodyPower) / (SPEC_HEAT_ALUMINIUM * MASS_BOILER_SHELL / 2.0);
        bodyTemp += deltaTime * (shellToBodyPower + elementToBodyPower) / HEAT_CAPACITY_BODY;

        // every two seconds, work out the average power by which shellTemp diverged from readTemperature
        static double accumulationPeriod = 0.0;
        static double shellTempAccumulatedError = 0.0;
        accumulationPeriod += deltaTime;
        shellTempAccumulatedError += readTemperature - shellTemp;
        shellTemp = readTemperature;

        if (waterTemp <= 95.0)
        {
          steamValveOpen = false;
          accumulationPeriod = 0.0;
          shellTempAccumulatedError = 0.0;
        }
        else if (accumulationPeriod >= 2.0)
        {
          double divergencePower = shellTempAccumulatedError * SPEC_HEAT_ALUMINIUM * MASS_BOILER_SHELL / 2.0 / accumulationPeriod;
          if (steamValveOpen && divergencePower > 100.0 || !steamValveOpen && divergencePower < -100.0)
            steamValveOpen = !steamValveOpen;
          accumulationPeriod = 0.0;
          shellTempAccumulatedError = 0.0;
        }

        // model the temperature of the control triac
        const double pcbTemp = AnalogIo::getPcbTemperature();
        triacTemp += (heaterPower / MAX_HEATER_POWER * MAX_TRIAC_POWER - (triacTemp - pcbTemp) * TRIAC_JUNCTION_AMBIENT_XFER_COEFF) * deltaTime / TRIAC_HEAT_CAPACITY;

        double desiredAverageShellTemp = tempSetpoint;
        if (tempSetpoint < 100.0)
        {
          // we want the water to reach target temperature in the next 15s so calculate the necessary average temperature of the shell
          double desiredWaterInputPower = (tempSetpoint - waterTemp) * SPEC_HEAT_WATER_100 * BOILER_VOLUME / 15.0;
          desiredWaterInputPower += waterToFlowPower;
          desiredAverageShellTemp = waterTemp + desiredWaterInputPower / BOILER_WATER_XFER_COEFF_NOFLOW;
          if (flowRate > 1.0)
            desiredAverageShellTemp = waterTemp + desiredWaterInputPower / 25.0;
          // now clip the temperature so that it won't take more than 20s to lose excess heat to ambient
          double maxStableAverageShellTemp = (brewHeadToAmbientPower * 20.0 - (waterTemp - tempSetpoint) * SPEC_HEAT_WATER_100 * BOILER_VOLUME) / SPEC_HEAT_ALUMINIUM / MASS_BOILER_SHELL + tempSetpoint;
          desiredAverageShellTemp = min(desiredAverageShellTemp, maxStableAverageShellTemp);
        }
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

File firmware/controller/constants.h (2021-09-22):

/*
 *     Copyright (C) 2010-2020 Tom Brazier (http://tomblog.firstsolo.net)
 *     
 *     This file is part of Hot Metal Brewbot.
 *     
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
 *     You should have received a copy of the GNU General Public License
 *     along with Hot Metal Brewbot .  If not, see <https://www.gnu.org/licenses/>.
 */

#ifndef COFFEEID_CONSTANTS_H
#define COFFEEID_CONSTANTS_H

#include <Arduino.h>

// Code modules to compile: by selecting fewer modules, it is possible to get the controller or
// calbration code to fit into an ATmega168 or just save upload time whilst developing.
#define CALIBRATION_CODE                          // define to include calibration code
#define CONTROLLER_CODE                           // define to implement the actual controller algorithms
#define REPORTING_CODE                            // define to include status reporting over the serial port

// operating parameters
static const double BREW_SETPOINT = 97.0;       // °C
static const double STEAM_SETPOINT = 166.0;     // °C average boiler temperature (bearing in mind element sides are a hotter and other sides cooler)
static const double MAX_FLOW_RATE = 10.0;       // ml/s well over what the pump can produce just to be sure
static const double BREW_FLOW_RATE_2CUP = 3.5;  // ml/s
static const double BREW_FLOW_RATE_1CUP = 2.5;  // ml/s half of BREW_FLOW_RATE_2CUP would be good, but it's a little close to the flow meter's min rate
static const double MIN_FLOW_RATE = 2.0;        // ml/s where the flow rate begins to be able to be controlled
static const double BREW_VOLUME_2CUP = 105.0;   // ml
static const double BREW_VOLUME_1CUP = 60.0;    // ml
static const double MIN_RESERVOIR_VOLUME = 100.0;// ml
static const unsigned INACTIVITY_TIMEOUT = 1200;// seconds with no activity before stopping heating activating the buzzer (20 minutes)
static const unsigned long BACKFLUSH_STALL_TIME = 1000000l; // microseconds to wait for while pump is stalled before flushing
static const unsigned long BACKFLUSH_FLUSH_TIME = 2500000l; // microseconds to wait for while pump is flushing before restarting
static const double STEAM_PUMP_PULSE_TEMP = 140.0;// temperature at which pulsing the pump begins in steam mode.
static const double STEAM_PUMP_PULSE_DUTY = 0.12;// duty cycle for pulsing the pump in steam mode.

// physical charcteristics of the AVR's internal temperature probe and circuitry
static const double PCBTEMP_OFFSET = 352.0;               // °C the offset to subtract to get the PCB's temperature once the AVR's self-heating is complete
static const double BANDGAP_VOLTAGE = 1.1;                // V nominal bandgap voltage from the datasheet
static const double AVRTEMP_FACTOR = 1.0e3;               // °C/V the ratio of ADC reading to temperature, from the datasheet
static const double AREF_VOLTAGE = 1.8;                   // V the voltage on the AREF pin

// physical characteristics of temperature probes 1 to 3 and their circuitry
static const double PT100_A = -0.00005775;
static const double PT100_B = 0.39083;
static const double PT100_C = 100.0;
static const double KTYPE_TEMPS[] = {0,10,20,30,40,50,60,70,80,90,100,110,120,130,140,150,160,170,180,190,200};                                                   // °C
static const double KTYPE_VOLTAGES[] = {0,0.397,0.798,1.203,1.612,2.023,2.436,2.851,3.267,3.682,4.096,4.509,4.92,5.328,5.735,6.138,6.54,6.941,7.34,7.739,8.138};  // mV
static const double VCC_VOLTAGE = 5.09;                   // V the arduina 5V regulator may not yield exactly 5V
//#define PROBE1_KTYPE
//static const double VOLTAGE_FACTOR1 = 1.8 / 1024 / (3.3e6 / 9.88e3);  // V linear function mapping from ADC reading to probe voltage
//static const double VOLTAGE_OFFSET1 = 0.129e-3;                       // ...
#define PROBE1_PT100
static const double RESISTANCE_FACTOR1 = 0.05;              // linear function mapping from ADC reading to resistance
static const double RESISTANCE_OFFSET_LOWRANGE1 = 93.77;    // ...
static const double RESISTANCE_OFFSET_HIGHRANGE1 = 116.85;  // ...
#define PROBE2_PT100
static const double RESISTANCE_FACTOR2 = 0.05;              // linear function mapping from ADC reading to resistance
static const double RESISTANCE_OFFSET_LOWRANGE2 = 94.05;    // ...
static const double RESISTANCE_OFFSET_HIGHRANGE2 = 117.54;  // ...
#define PROBE3_NTC
static const double VOLTAGE_FACTOR3 = 3.1e-3;               //  linear function mapping from ADC reading to voltage
static const double VOLTAGE_OFFSET_LOWRANGE3 = 2.16;        // ...
static const double VOLTAGE_OFFSET_HIGHRANGE3 = 2.7;        // ...
static const double SERIES_R3 = 4.68e3;                     // Ohms the resistance of the resistor in series with the probe
static const double R25_3 = 106e3;                          // Ohms the resistance of the NTC probe at 25°C
static const double BETA3 = 3950.0;                         // the beta value of the NTC probe
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

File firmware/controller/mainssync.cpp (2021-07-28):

/*
 *     Copyright (C) 2010-2020 Tom Brazier (http://tomblog.firstsolo.net)
 *     
 *     This file is part of Hot Metal Brewbot.
 *     
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
 *     You should have received a copy of the GNU General Public License
 *     along with Hot Metal Brewbot .  If not, see <https://www.gnu.org/licenses/>.
 */

#include "mainssync.h"
#include "constants.h"

#include <Arduino.h>

static volatile double g_mainsCycleLength = MAINS_CYCLE_LENGTH;
static volatile double g_pumpPower = 0.0;
static volatile uint16_t g_pumpDutyCycle = 0;
static volatile int16_t g_energyAvailPerHalfCycle = 0.0;  // integer value representing real number * 256
static volatile int16_t g_energyReqdPerHalfCycle = 0.0;   // integer value representing real number * 256

static inline uint16_t encodeReal(double val) {return val * 256;}
static inline uint16_t roundReal(uint16_t val) {return (val + (1<<7)) >> 8;}

// invoked at mains voltage zero-crossing
ISR(PCINT2_vect)
{
  bool polarity = digitalRead(MAINS_POLARITY_PIN);

  // eliminate very fast noise that changes the input twice before the ISR can respond
  static bool expected = true;
  if (polarity != expected)
    return;
  expected = !expected;

  // if this is a zero-crossover heading towards positive (i.e. if pin is low) then the signal
  // edge from the mains crossing circuit is sharper, so use this as our zero-crossing reference
  if (!polarity)
  {
    // if the time since last trigger is more than 20% off from expected mains mains cycle length, reject this as noise
    static uint32_t lastTime = 0;
    uint32_t now = micros();;
    int32_t microsSinceLastTime = now - lastTime;
    lastTime = now;
    if (abs(microsSinceLastTime - int32_t(MAINS_CYCLE_LENGTH * 1000000)) < uint32_t(MAINS_CYCLE_LENGTH * 1000000 * 0.2))
    {
      // make sure TCNT2 flips over to zero at least 1 tick before mains zero-crossing
      static const uint8_t expectedTcnt2 = 2 + (MAINS_CROSS_LATENCY * F_CPU / 1024);
      TCNT2 = expectedTcnt2;

      // update our record of the mains cycle length, keeping a running average
      g_mainsCycleLength = 0.8 * g_mainsCycleLength + 0.2e-6 * microsSinceLastTime;

      // and update the range of TCNT2
      const double ocr2a = g_mainsCycleLength / 2 * (F_CPU / 1024) - 1;
      OCR2A = ocr2a + 0.5;
    }
  }
}

// once the AC phase measurement is stabilised, timer2 overflows just about at zero crossover
ISR(TIMER2_OVF_vect)
{
  // Keep track of two numbers:
  //   First: the energy that has been delivered minus the energy that has been requested.
  //   Second: the energy that has been delivered in this half-cycle minus that delivered in the other.
  static int16_t energyError = 0;     // +ve means more energy has been delivered than requested
  static int16_t cycleDelta = 0;      // +ve means this half-cycle has delivered the most energy

  // if there is an energy deficit and this cycle has generated less energy than the other cycle
  // then switch on for this cycle
  if (g_energyReqdPerHalfCycle > 0 && energyError <= 0 && cycleDelta <= 0)
  {
    digitalWrite(BOILER_POWER_PIN, true);
    energyError += g_energyAvailPerHalfCycle;
    cycleDelta += g_energyAvailPerHalfCycle;
  }
  else
    digitalWrite(BOILER_POWER_PIN, false);

  // reduce the total error by what should have been delivered
  energyError -= g_energyReqdPerHalfCycle;

  // flip the value of cycleDelta because the next time this function is called will be for the other half-cycle
  cycleDelta = -cycleDelta;

  // only change pump state every second half-cycle
  static bool thisHalfCycle = true;
  if (thisHalfCycle)
  {
    static int16_t excessCyclesPumped = 0;
    if (g_pumpDutyCycle > 0 && excessCyclesPumped <= 0)
    {
      digitalWrite(PUMP_POWER_PIN, true);
      excessCyclesPumped += encodeReal(1.0);
    }
    else
      digitalWrite(PUMP_POWER_PIN, false);

    excessCyclesPumped -= g_pumpDutyCycle;
  }
  thisHalfCycle = !thisHalfCycle;
}
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

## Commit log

2021-07-28 initializing repository with rev 2.0 plus some modifications
    [DoubleBoilerPower.sch, GaggiaBabyClassWiring.sch, hotmetal.brd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]
2021-07-29 Added schematic PDFs of PCB releases for quick reference
2021-09-22 Implemented flow meter calibration and recalibrated flow meter (getting quite a different curve)
2021-09-22 Also track flow meter pulses in serial output

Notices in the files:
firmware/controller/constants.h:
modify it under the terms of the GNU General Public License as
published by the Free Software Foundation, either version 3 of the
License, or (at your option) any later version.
